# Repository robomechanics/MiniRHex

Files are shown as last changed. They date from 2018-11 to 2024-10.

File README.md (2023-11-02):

# MiniRHex: An Open-Source Hexapod Robot

[Contact Info](https://www.cmu.edu/me/robomechanicslab/contact.html)

MiniRHex is a miniature-scale hexapod designed by the [Robomechanics Lab](https://www.cmu.edu/me/robomechanicslab/) based on the design of the cockroach-inspired [RHex](https://repository.upenn.edu/handle/20.500.14332/34172). Notable features include a 3D printed chassis and legs for low cost construction and an intuitive software package that allows for highly-customizable control over the robot’s behavior. MiniRHex is designed to be an educational and outreach tool enabling students to experiment with a fully functional walking robot at a much lower cost. The low price tag lets research groups maintain a fleet of machines, allowing each student more hands-on interaction with the hardware. Possible educational principles include gait design and optimization, leg design and control, and mobile robot sensor incorporation.

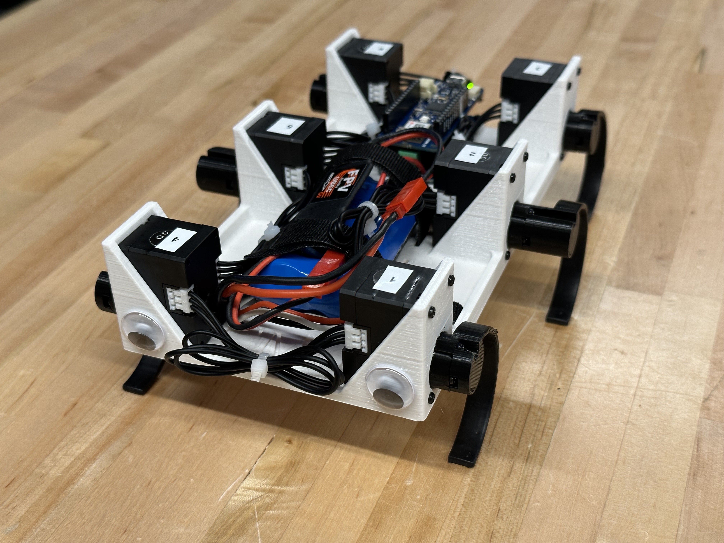
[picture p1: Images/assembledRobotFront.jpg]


# Setup Instructions
Building a MiniRHex requires access to a 3D printer. The links for off the shelf parts can be found below.

## Acquire Parts
The Parts List and Links to order can be found in [Parts List](HardwareList).

## Assemble Robot
Assembly Instructions are available at [Assembly Instructions](Assembly).

## Install Software
1. Install the Arduino IDE from https://www.arduino.cc/en/software
2. Open the Arduino IDE and under "Tools" select "Manage Libraries..."
   - Type "DynamixelShield" into the search bar
   - Select "Install" for the DynamixelShield library
3. Under "Tools" hover over "Board" and select "Boards Manager..."
   - Type "Arduino SAMD Boards" into the search bar
   - Select "Install" for the Arduino SAMD Boards (32-bits ARM Cortex-M0+)
4. (Non-developers) Download the [MiniRHex repository](https://github.com/robomechanics/MiniRHex/archive/refs/heads/main.zip) and extract the downloaded zip file
5. (Developers) Clone the MiniRHex repository from https://github.com/robomechanics/MiniRHex.git

# Operating Instructions
## Upload Code
1. Connect the MiniRHex to your computer via the Micro USB port
2. Open MiniRHex.ino (located in the MiniRHex subfolder) in the Arduino IDE and check that under "Tools":
   - "Board" is set to "Arduino MKR WiFi 1010" (under "Arduino SAMD (32-bits ARM Cortex-M0+) Boards")
   - "Port" is set to the correct COM port, e.g. "COM# (Arduino MKR WiFi 1010)"
3. Upload code to the robot (the circular button near the top left with an arrow pointing to the right)
4. Insert a fully charged battery, fasten the velcro straps, connect the voltage monitor, and connect the battery cable
5. Open the Serial Monitor in the Arduino IDE (the circular button in the top right with a magnifying glass)
6. Type "w" into the text box and hit enter to start walking! ("q" to stop, "s" to reverse", "a" to turn left, "d" to turn right)
7. To modify the walking gait, go to the "gait_parameters.cpp" tab in the Arduino IDE and edit the parameters for each leg, then upload code again (see comments in the file for more details)
8. When finished, unplug the battery and store it in a fireproof container (never leave a battery in the robot!)

## Connect to Wi-Fi
1. After uploading code, the LED on the Arduino will turn green and the Serial monitor should initially print the following message:
> Starting WiFi network...  
> SSID: minirhex    
> Website: http://10.0.0.1
2. Connect to the wifi network listed after "SSID" from your phone or computer. The LED on the Arduino will turn blue and start flashing.
3. On your device, navigate to the provided website. Make sure to use http, not https.
4. Use the buttons or the indicated keys to wirelessly control the robot!

# Robot Specifications
| | MiniRHex | X-RHex (2010) |
|---|---|---|
| Mass | 0.40 kg | 8.6 kg |
| Carrying Capacity [^1]| 1.8-3 kg | 5-10 kg |
| Length | 0.186 m | 0.53 m |
| Width | 0.100 m | 0.39 m |
| Leg Diameter | 0.064 m | 0.175 m |
| Leg Spring Constant | 0.3 N/mm | 1.4-1.7 N/mm |
| Leg Actuation | Dynamixel XL330 Servo | Maxon Brushless Motor |
| Onboard Processor | Arduino MKR WiFi 1010 | PC104, Intel Atom |
| Single Unit Price | <$300 | ~$20,000 |

[^1]: Evaluated using legs with higher spring constant

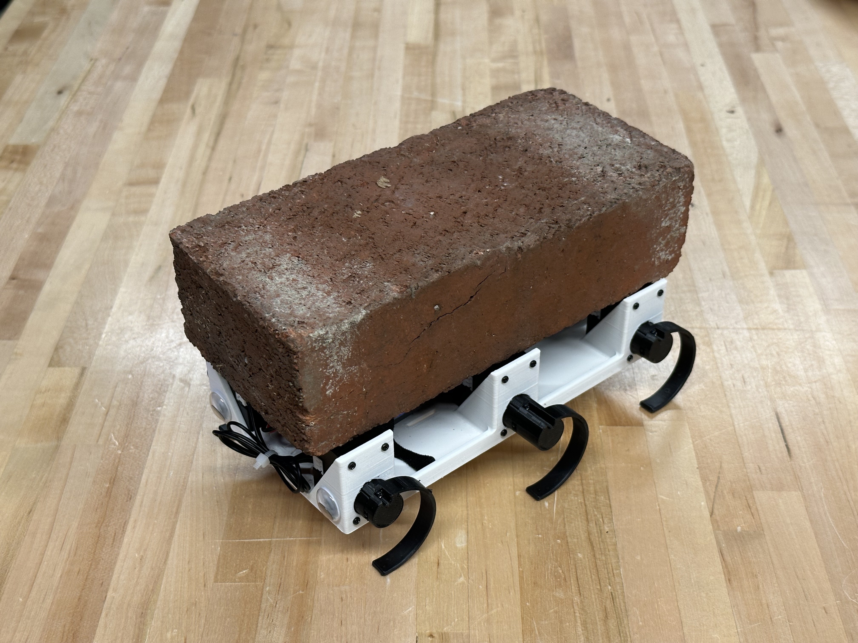
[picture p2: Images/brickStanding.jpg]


# Useful Links
### Parts List
The part list can be found at [Parts List](HardwareList).
### MiniRHex Repository
The MiniRHex repository can be found at [MiniRHex Repository](https://github.com/robomechanics/MiniRHex.git).
### Cite MiniRHex
If referencing MiniRHex in a paper, please cite [this abstract](http://www.andrew.cmu.edu/user/amj1/papers/RSS2018ws_MiniRHex.pdf).
Use [this BibTeX](/citation.txt) for citations:
> M. Barragan, N. Flowers, and A. M. Johnson. "MiniRHex: A Small, Open-source, Fully Programmable Walking Hexapod". In *Robotics: Science and Systems Workshop on ``Design and Control of Small Legged Robots''*, Pittsburgh, PA, June 2018.

### Images
See the [image gallery](Images) for more MiniRHex pictures.
        
### Videos
Check out the Robomechanics Lab [YouTube Page](https://www.youtube.com/watch?v=ldLXVDNCCzc&list=PLxHmBiQi0bD2aFgPKIrXhYXCCOGhTQmmk) for videos of MiniRHex in action!

# Contributors
MiniRHex was designed by the following people in the [Robomechanics Lab](https://www.cmu.edu/me/robomechanicslab/)
* Nikolai Flowers (BS ME '20)
* Barrett Werner (MS ME '19)
* Monica Barragan (BS ME '19)
* Cameron Selby (MS ME '18)
* Scott Phillips (BS ME '20)
* J. Joe Payne (Ph.D ME)
* Joe Norby (Ph.D ME '22)
* Catherine Pavlov (Ph.D ME '23)
* Paul Nadan (Ph.D RI)
* Aaron Johnson (Advisor)

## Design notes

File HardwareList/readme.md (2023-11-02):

# Hardware List

| Supplier | Item | Quantity | Price | Link |
|---|---|---|---|---|
| **Amazon** | Arduino MKR WiFi 1010  | 1 | $39.99 | [Amazon](https://www.amazon.com/Arduino-MKR-WiFi-1010-ABX00023/dp/B07FYFF5YZ) |
| | Batteries and charger  | 1 (2 batteries) | $22.99 | [Amazon](https://www.amazon.com/1500mAh-Li-ion-Battery-Helicopter-Charger/dp/B089W89KCP) |
| | Plastidip | 1 (per 5 robots) | $19.00 | [Amazon](https://www.amazon.com/Plasti-Dip-Multi-Purpose-Coating-Aerosol/dp/B07QCPXXBV) |
| | JST Plug Connectors | 1 (per 10 robots) | $6.29 | [Amazon](https://www.amazon.com/eBoot-Connector-Female-Cable-Battery/dp/B01M5AHF0Z) |
| | 5V UBEC | 1 (per 2 robots) | $11.69 | [Amazon](https://www.amazon.com/ShareGoo-Converter-Module-Quadcopter-Holder/dp/B07DYXTX9H) |
| | 8"x1/2" Velcro Straps  | 1 (per 8 robots) | $8.18 | [Amazon](https://www.amazon.com/VELCRO-Brand-Reusable-Fastening-Organizing/dp/B0006BB9MG) |
| | LiPo Voltage Monitor | 1 | $5.49 | [Amazon](https://www.amazon.com/Battery-Monitor-Voltage-Checker-Indicator/dp/B013U1CP08) |
| | LiPo Safe Bag | 1 (per 8 batteries) | $10.99 | [Amazon](https://www.amazon.com/DerBlue-Fireproof-Explosionproof-Battery-Bag185x75x60mm/dp/B01GCHBQJS/) |
| **Robotis** | Arduino Shield | 1 | $19.10 | [Robotis](https://www.robotis.us/dynamixel-shield-for-arduino-mkr-series/) |
| | Dynamixel XL330-M077-T | 6 | $143.40 | [Robotis](https://www.robotis.us/dynamixel-xl330-m077-t/) |
| **3D Print** | Robot Body | 1 | | [STL File](../CAD/STL/robot_body.STL) |
| | Front & Rear Left Legs | 2 | | [STL File](../CAD/STL/standard_leg_left.STL) |
| | Front & Rear Right Legs| 2 | | [STL File](../CAD/STL/standard_leg_right.STL) |
| | Middle Left Leg | 1 | | [STL File](../CAD/STL/standard_leg_left_middle.STL) |
| | Middle Right Leg | 1 | | [STL File](../CAD/STL/standard_leg_right_middle.STL) |
| | PLA Filament | ~120g PLA | ~$3.00 | [Amazon](https://www.amazon.com/HATCHBOX-3D-Filament-Dimensional-Accuracy/dp/B015I1CZUI) |
| **Total Cost** | | 1 robot | **$290.12** | (as of 10-27-23) |

[Return to homepage](../).

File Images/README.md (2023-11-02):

# MiniRHex Image Gallery

MiniRHex Front View

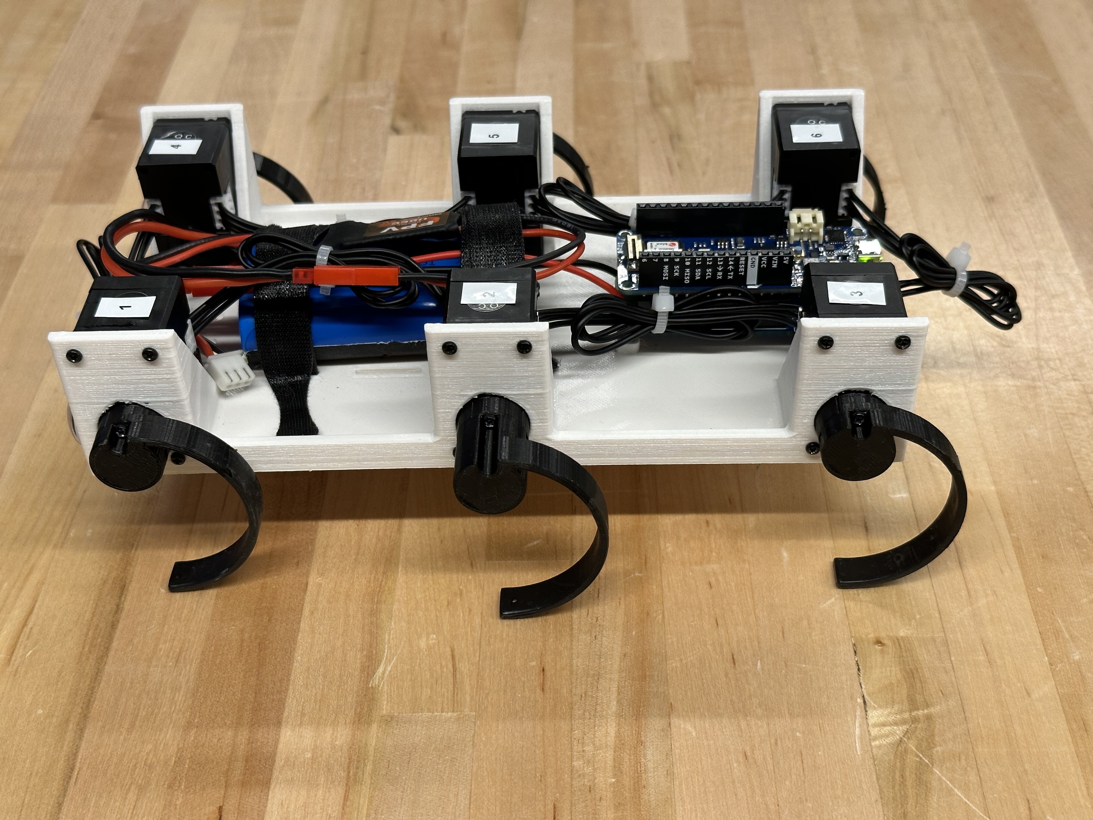
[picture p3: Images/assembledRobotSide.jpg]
MiniRHex Side View


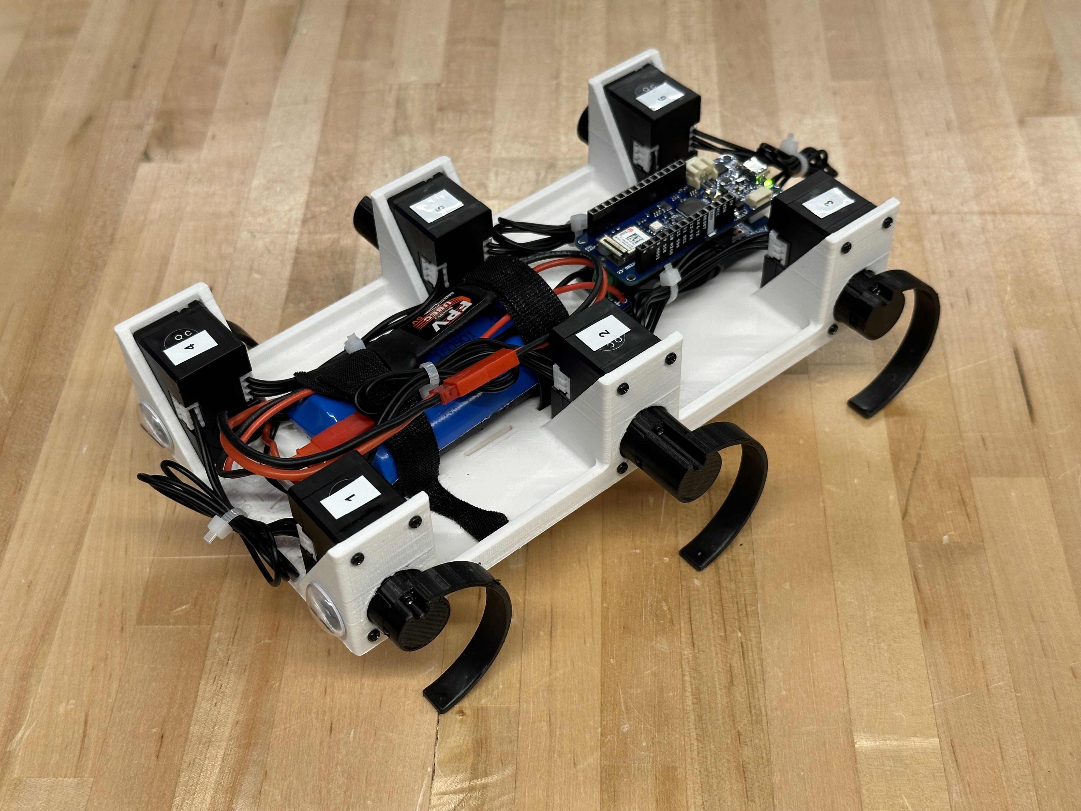
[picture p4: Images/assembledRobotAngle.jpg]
MiniRHex Above View


MiniRHex Carrying Brick

[Return to homepage](../).

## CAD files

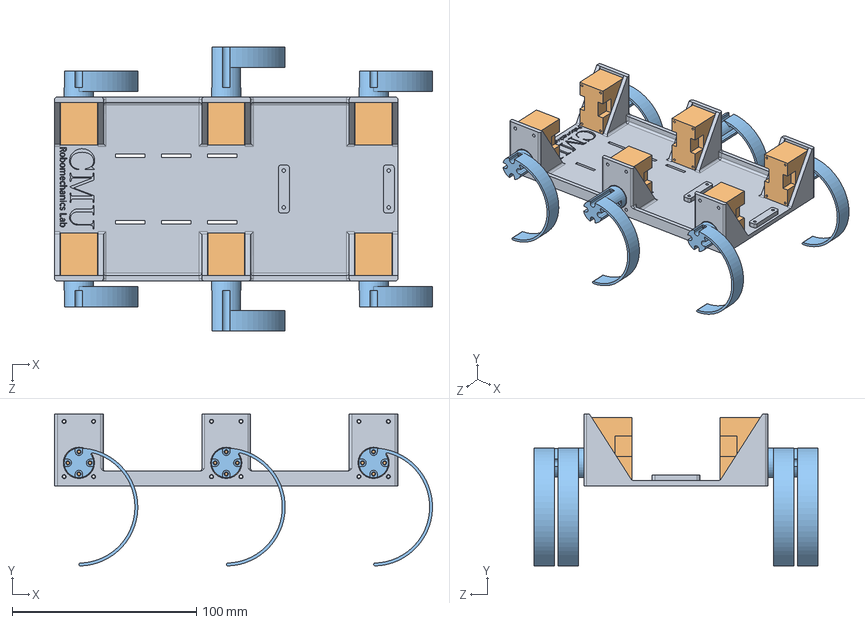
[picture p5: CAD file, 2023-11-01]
CAD/minirhex_assembly.SLDASM
205.2 x 82.5 x 154.0 mm
robot_body
dxl_XL-330 x 6
standard_leg x 6

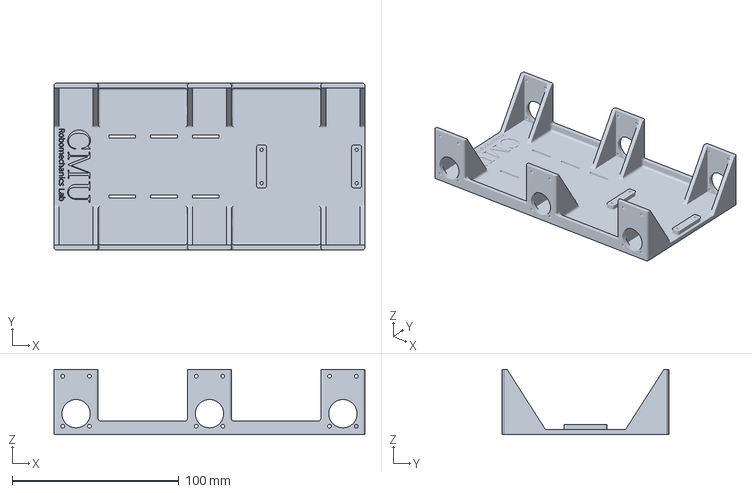
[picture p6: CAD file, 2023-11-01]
CAD/Prusa/robot_body.3mf
186.5 x 100.0 x 39.0 mm

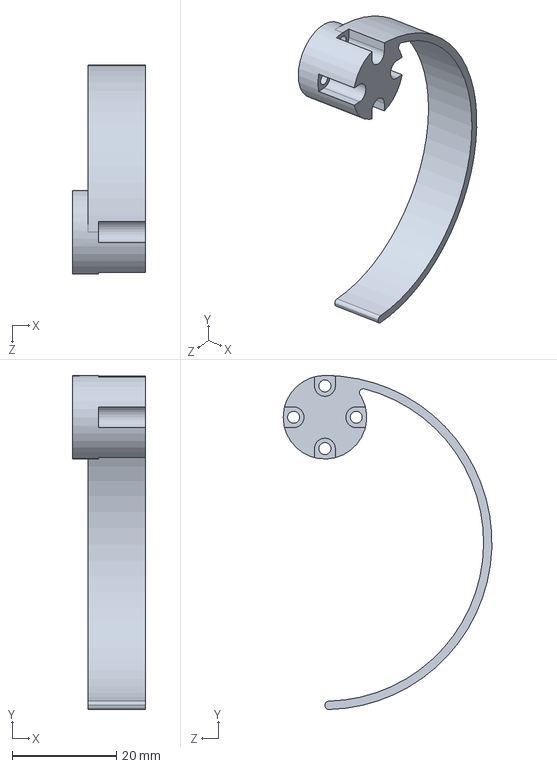
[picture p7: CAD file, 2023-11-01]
CAD/standard_leg.SLDPRT
14.0 x 64.0 x 40.0 mm

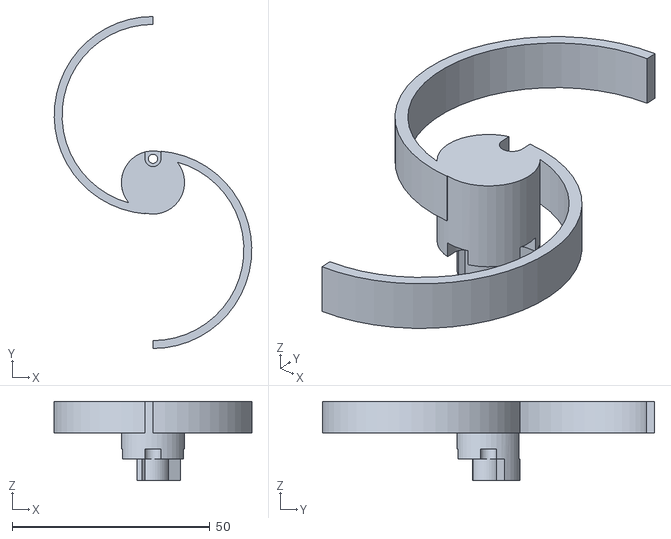
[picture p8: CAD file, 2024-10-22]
CAD/STL/quick_connect_leg_double_middle_left.STL
50.0 x 84.0 x 20.0

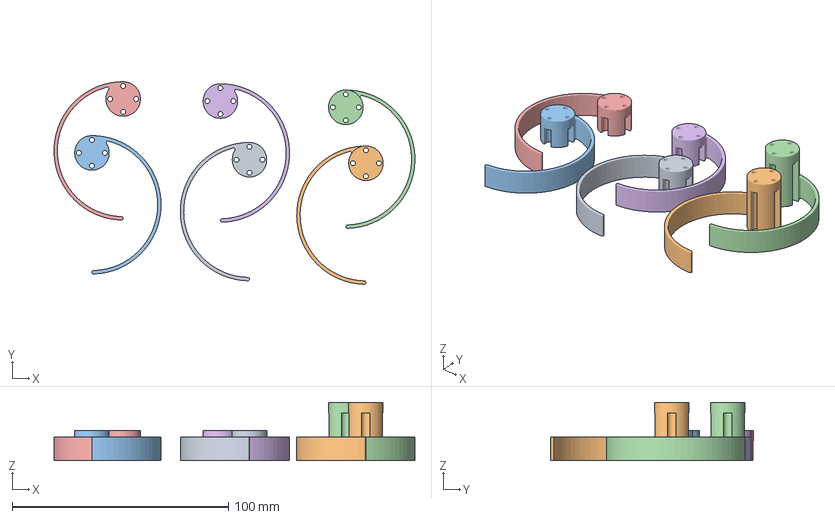
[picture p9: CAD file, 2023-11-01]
CAD/Prusa/standard_legs.3mf
166.9 x 93.7 x 27.0 mm
standard_leg_left.STL x 2
standard_leg_left_middle.STL
standard_leg_right.STL x 2
standard_leg_right_middle.STL

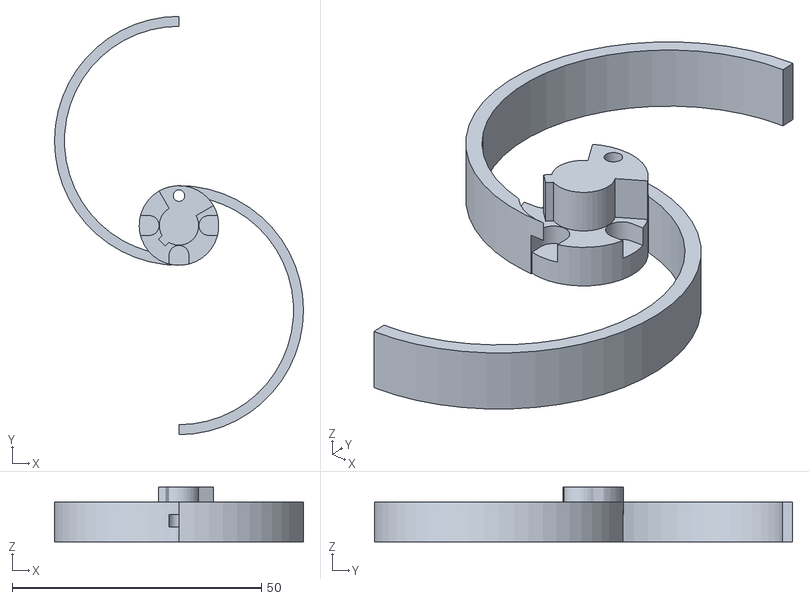
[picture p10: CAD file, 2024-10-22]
CAD/STL/quick_connect_leg_double_right.STL
50.0 x 84.0 x 11.0

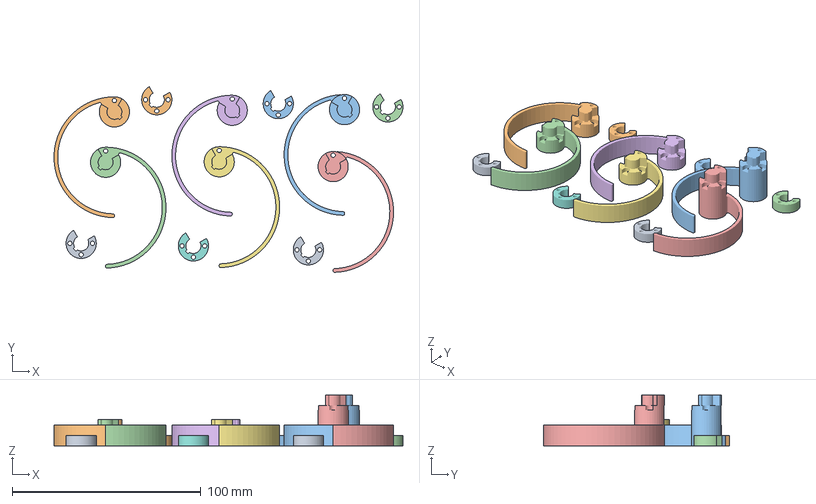
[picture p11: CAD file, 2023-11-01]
CAD/Prusa/quick_connect_legs.3mf
184.8 x 98.3 x 27.0 mm
quick_connect_hub.STL x 6
quick_connect_leg_left.STL x 2
quick_connect_leg_left_middle.STL
quick_connect_leg_right.STL x 2
quick_connect_leg_right_middle.STL

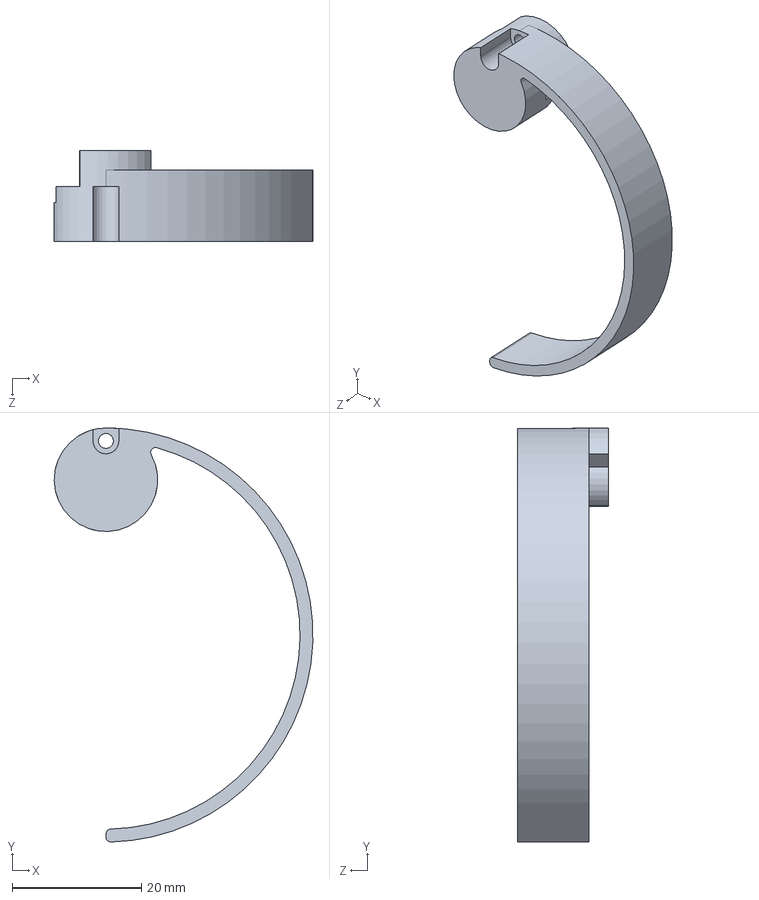
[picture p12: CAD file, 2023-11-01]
CAD/quick_connect_leg.SLDPRT
40.0 x 64.0 x 14.0 mm

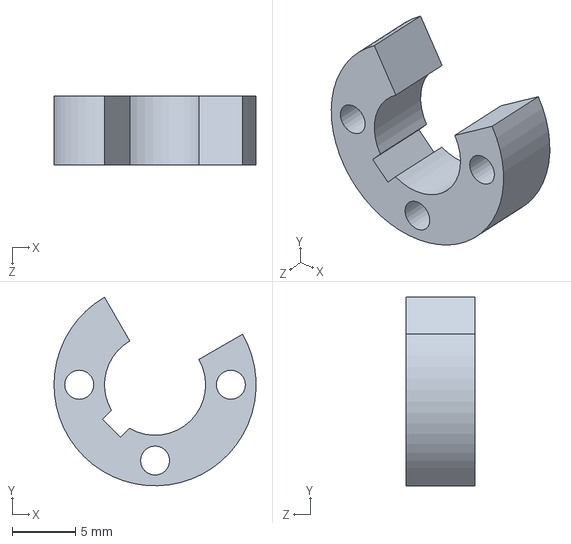
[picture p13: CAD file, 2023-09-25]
CAD/quick_connect_hub.SLDPRT
16.0 x 14.9 x 5.50 mm

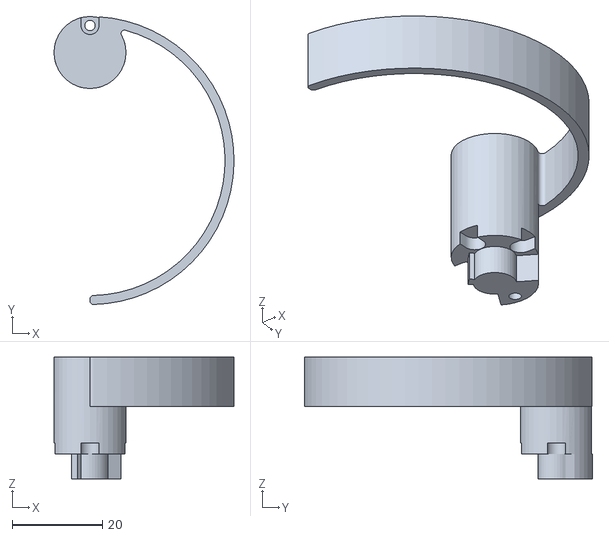
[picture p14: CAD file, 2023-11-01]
CAD/STL/quick_connect_leg_left_middle.STL
40.0 x 64.0 x 27.0

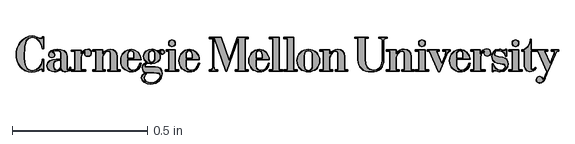
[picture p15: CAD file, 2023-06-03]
CAD/cmu-wordmark-horizontal-k.dxf
2.01 x 0.178 in

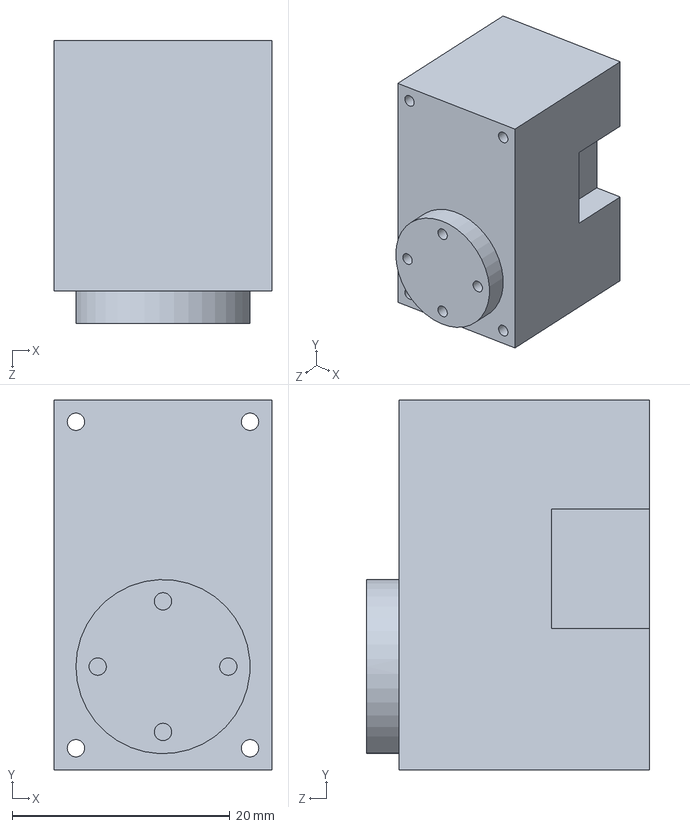
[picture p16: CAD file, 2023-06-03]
CAD/dxl_XL-330.SLDPRT
20.0 x 34.0 x 26.0 mm

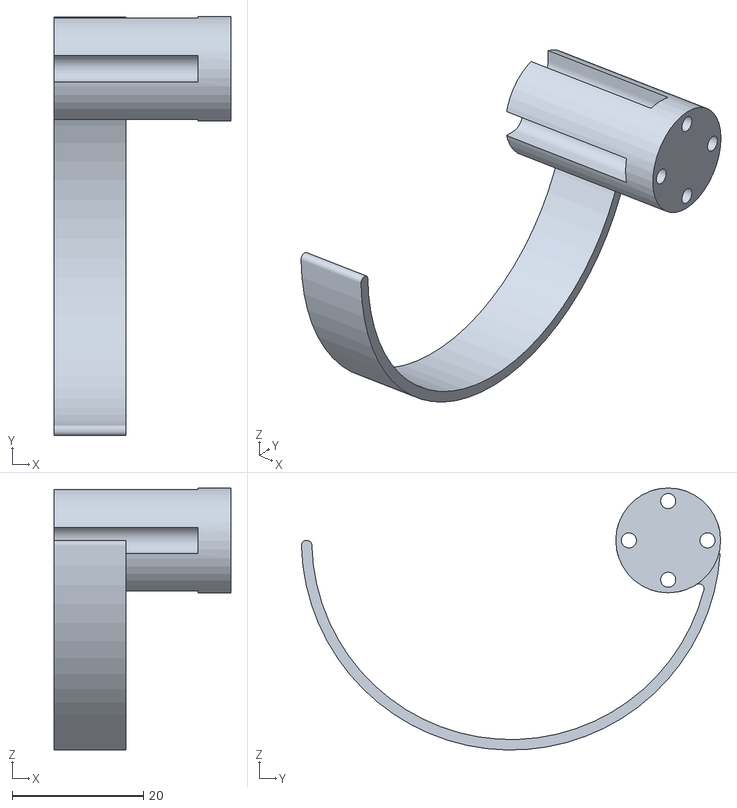
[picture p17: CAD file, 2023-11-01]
CAD/STL/standard_leg_right_middle.STL
27.0 x 64.0 x 40.0

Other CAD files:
CAD/quick_connect_leg_double.SLDPRT
CAD/STL/quick_connect_leg_double_left.STL
CAD/STL/quick_connect_leg_double_middle_right.STL
CAD/STL/quick_connect_leg_right_middle.STL
CAD/robot_body.SLDPRT
CAD/STL/quick_connect_hub.STL
CAD/STL/quick_connect_leg_left.STL
CAD/STL/quick_connect_leg_right.STL
CAD/STL/robot_body.STL
CAD/STL/standard_leg_left.STL
CAD/STL/standard_leg_left_middle.STL
CAD/STL/standard_leg_right.STL
CAD/rml-logo-robots-black.dxf

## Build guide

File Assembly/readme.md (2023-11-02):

# Preparation
1. Acquire the following equipment.
    * 3D printer + PLA filament
    * Wire cutters
    * Small Phillips head screwdriver
    * Small flat head screwdriver (basic users only)
    * Soldering station (advanced users only)

2. Purchase necessary components from the [Hardware List](../HardwareList).
    * Amazon: Arduino MKR, Battery, Plastidip, JST Connector, 5V UBEC, Velcro Straps, LiPo Voltage Monitor, and LiPo Safe Bag
    * Robotis: Dynamixel Servos, Arduino Shield

# Fabrication
1. 3D print the following parts. STL files can be found in [CAD/STL](https://github.com/robomechanics/MiniRHex/tree/main/CAD/STL) and SolidWorks files are provided in [CAD](https://github.com/robomechanics/MiniRHex/tree/main/CAD) to allow modification if needed. It is recommended to print with PLA, using the provided settings. Users of Prusa i3 MK3S 3D printers can also use the PrusaSlicer project files and g-code in the [CAD/Prusa](https://github.com/robomechanics/MiniRHex/tree/main/CAD/Prusa) folder. Make sure to remove any support material from the legs before assembly.

    * 1 robot body ([robot_body.STL](../CAD/STL/robot_body.STL)): 15%-20% infill, no supports
    * 2 standard left front/back legs ([standard_leg_left.STL](../CAD/STL/standard_leg_left.STL)): 100% infill, support on build plate
    * 2 standard right front/back legs ([standard_leg_right.STL](../CAD/STL/standard_leg_right.STL)): 100% infill, support on build plate
    * 1 standard left middle leg ([standard_leg_left_middle.STL](../CAD/STL/standard_leg_left_middle.STL)): 100% infill, support on build plate
    * 1 standard right middle leg ([standard_leg_right_middle.STL](../CAD/STL/standard_leg_right_middle.STL)): 100% infill, support on build plate

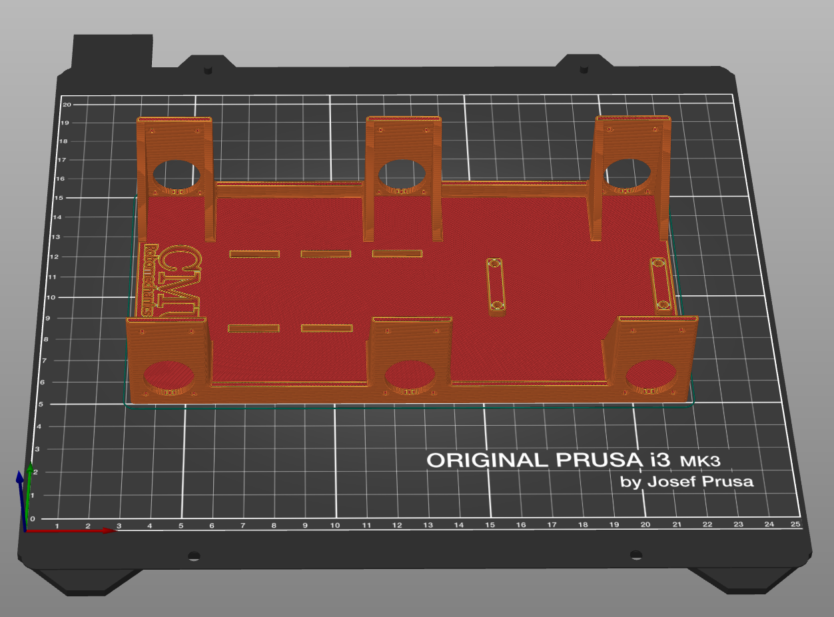
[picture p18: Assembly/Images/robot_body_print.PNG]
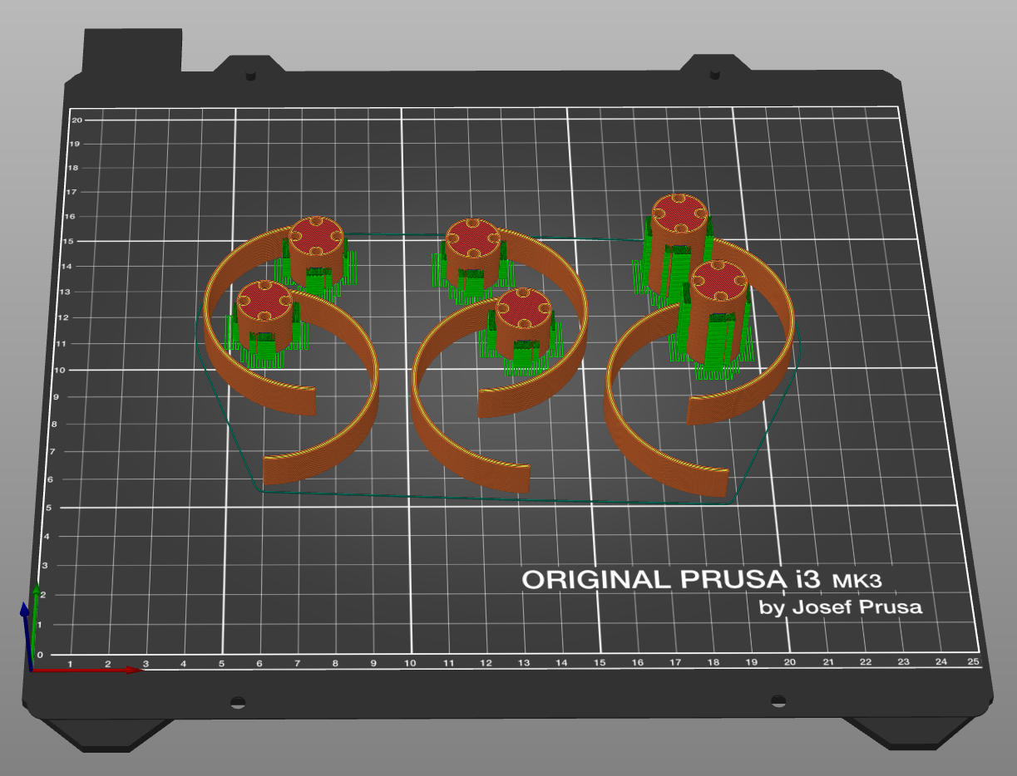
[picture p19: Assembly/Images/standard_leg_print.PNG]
      

    Certain users may desire to frequently switch out different legs, for which a quick-connect leg design is also available. The quick-connect legs are faster to swap, but less durable. Quick-connect leg users should instead print the following.

    * 1 robot body ([robot_body.STL](../CAD/STL/robot_body.STL)): 15%-20% infill, no supports
    * 2 quick-connect left front/back legs ([quick_connect_leg_left.STL](../CAD/STL/quick_connect_leg_left.STL)): 100% infill, support on build plate
    * 2 quick-connect right front/back legs ([quick_connect_leg_right.STL](../CAD/STL/quick_connect_leg_right.STL)): 100% infill, support on build plate
    * 1 quick-connect middle left leg ([quick_connect_leg_left_middle.STL](../CAD/STL/quick_connect_leg_left_middle.STL)): 100% infill, support on build plate
    * 1 quick-connect middle right leg ([quick_connect_leg_right_middle.STL](../CAD/STL/quick_connect_leg_right_middle.STL)): 100% infill, support on build plate
    * 6 quick-connect hubs ([quick_connect_hub.STL](../CAD/STL/quick_connect_hub.STL)): 100% infill, support on build plate

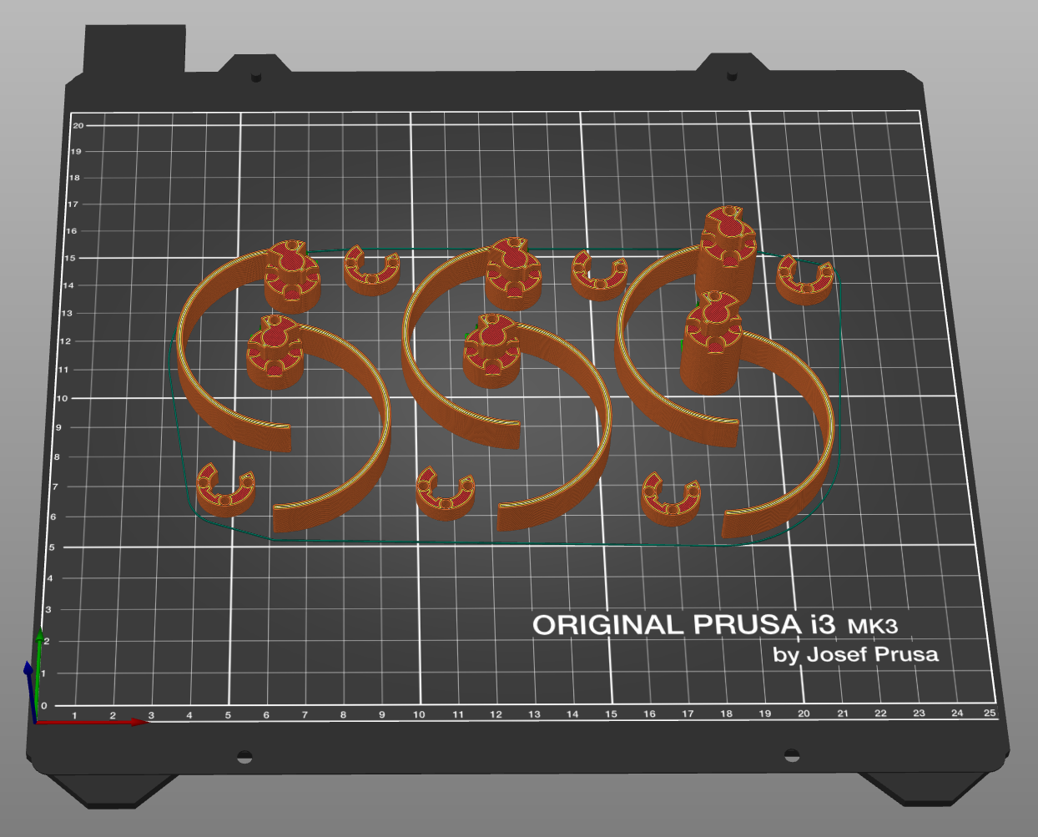
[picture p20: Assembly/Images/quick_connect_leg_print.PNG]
    

    Several additional leg variants exist, all compatible with the quick-connect system. For each additional set of legs you will need to 3D print 4 front/back legs and 2 middle legs of the appropriate type (but no additional hubs are needed).

2. Add Plastidip to legs for increased friction.
    * Use Plastidip (either dip or spray) to coat around 75% of each of the six legs until a high friction surface forms on each leg.
    * Between each coat, let dry for at least one hour.
    * Make sure the dip is evenly coated around the leg.
    * Do not cover the through holes for the screws.

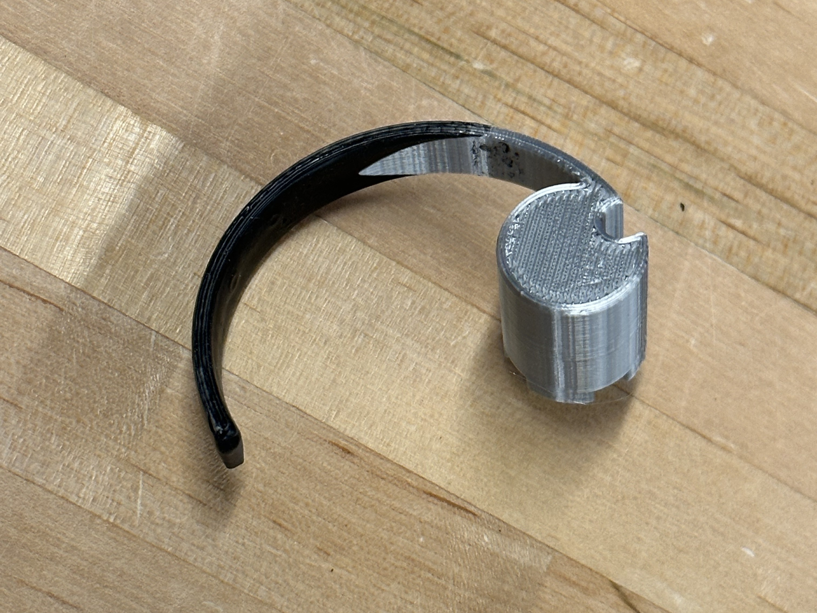
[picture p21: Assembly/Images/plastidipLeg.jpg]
    

# Assembly
1. Locate and sort motor screws.
    * Each of the motors comes with a set of screws. Open all six motor packages and sort into short and long screws.
    * You will need 4 short screws (M2x6) and 48 long screws (M2x8) to assemble the robot.
  
2. Mount the servos to the robot body.
    * Each motor requires 4 long screws. The screws will tap directly into the motor's plastic, so do not over tighten them.

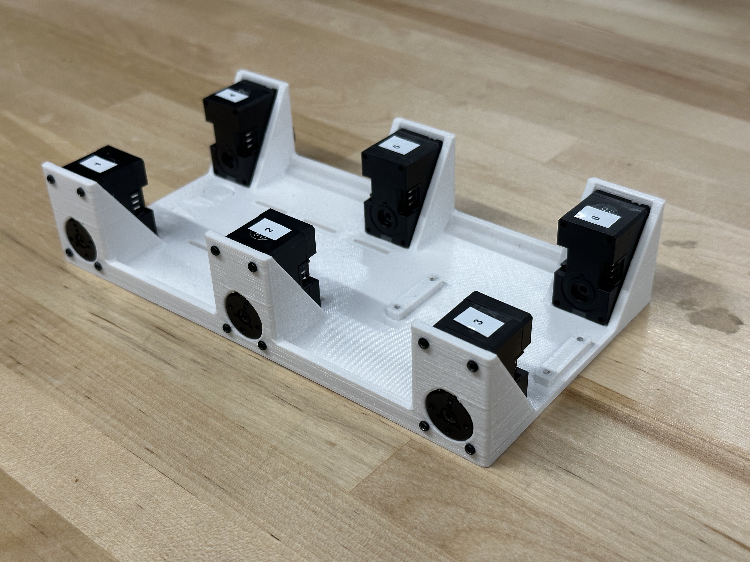
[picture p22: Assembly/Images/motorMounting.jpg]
    

3. Trim the leads on the Arduino shield.
    * The Robotis Arduino shield comes with leads that are too long. Using wire cutters, trim them to within 1-2mm of the board.
    * Only trim the leads on the shield, not the Arduino itself!

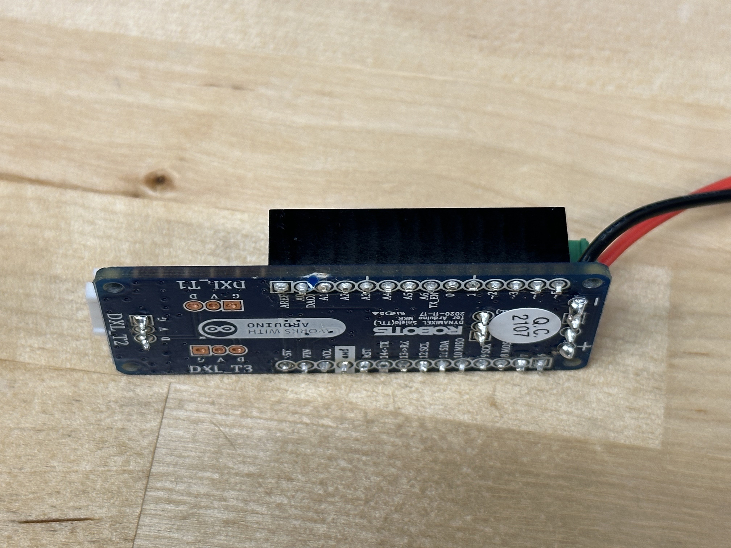
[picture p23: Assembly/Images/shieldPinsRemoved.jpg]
    

4. Attach the JST connector to the Arduino shield.
    * Basic users can insert the red and black wires into the green screw terminals (red goes into the + side, and black goes into the - side), then tighten them using the flat head screwdriver. Do not swap the colors, or it could severely damage the electronics!
    * Advanced users can instead solder the wires directly to the Arduino shield for a more robust connection, as pictured.

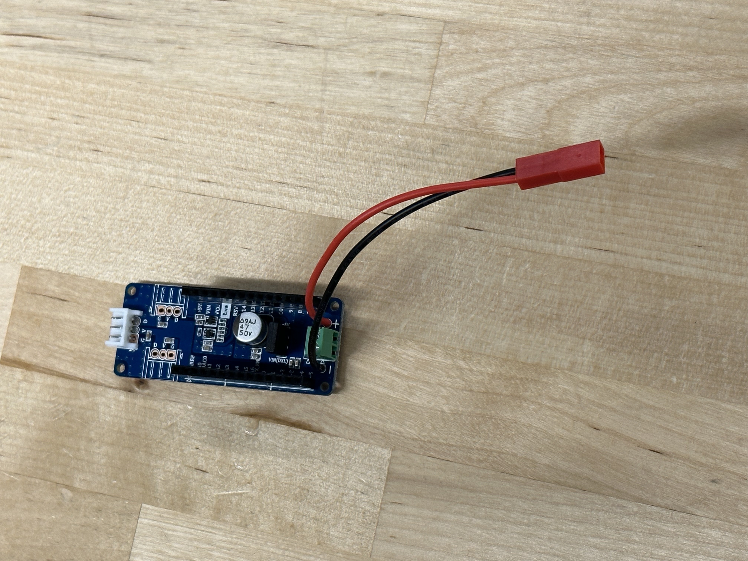
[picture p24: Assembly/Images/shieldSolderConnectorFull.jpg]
    

5. Mount the Arduino shield to the robot body.
    * You will needs 4 short screws. The screws will tap directly into the motor's plastic, so do not over tighten them.
    * The screw terminals and JST connector should face the center of the robot body.

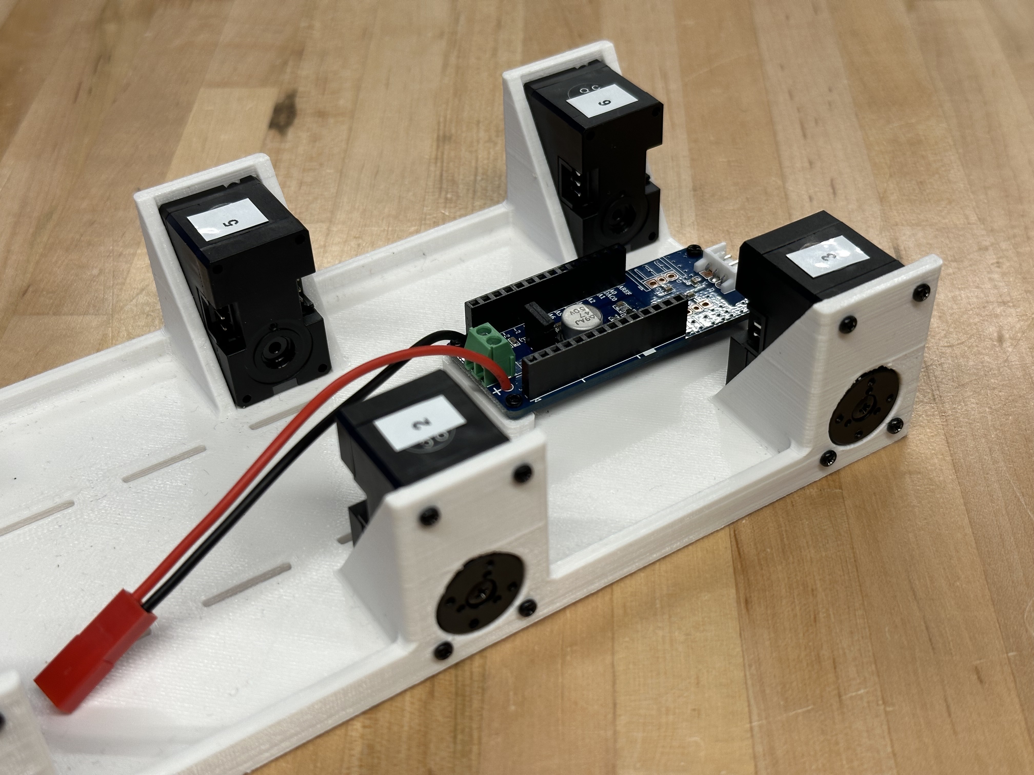
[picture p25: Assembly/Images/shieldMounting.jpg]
    

6. Stack the Arduino on top of the Arduino shield.
    * The header pins should line up, with the micro USB port facing the edge of the robot.

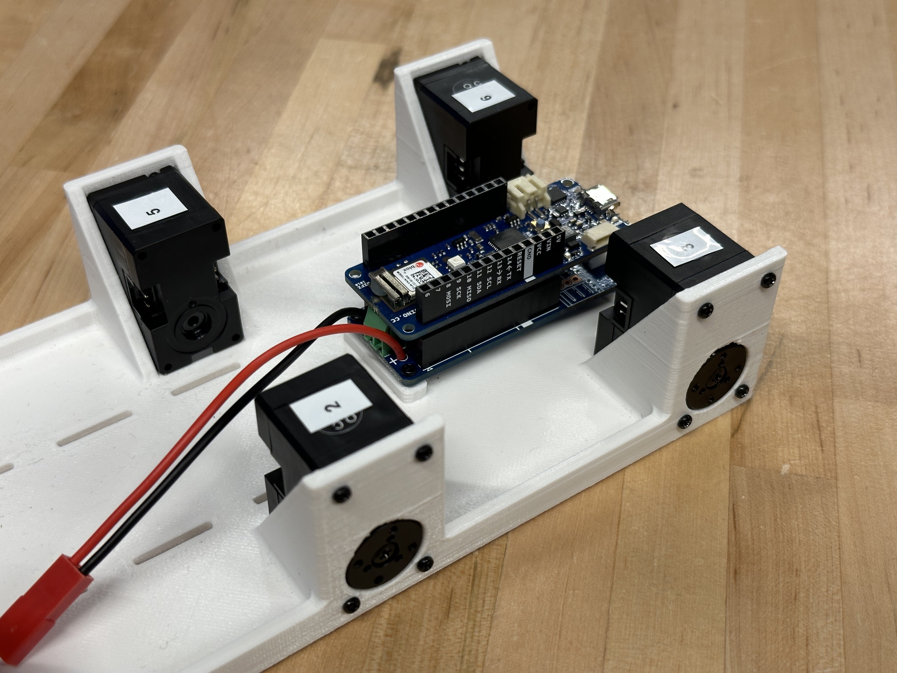
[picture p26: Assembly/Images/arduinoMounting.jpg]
    

7. Wire up the motors using the included Dynamixel cables.
    * The motors should be daisy-chained to each other in series, with the Arduino shield as one end of the chain.
    * A suggested ordering is: Arduino Shield -> Motor 6 -> Motor 5 -> Motor 4 -> Motor 1 -> Motor 2 -> Motor 3.
    * Use either the included wire wraps or zip ties to manage the wires, as pictured.

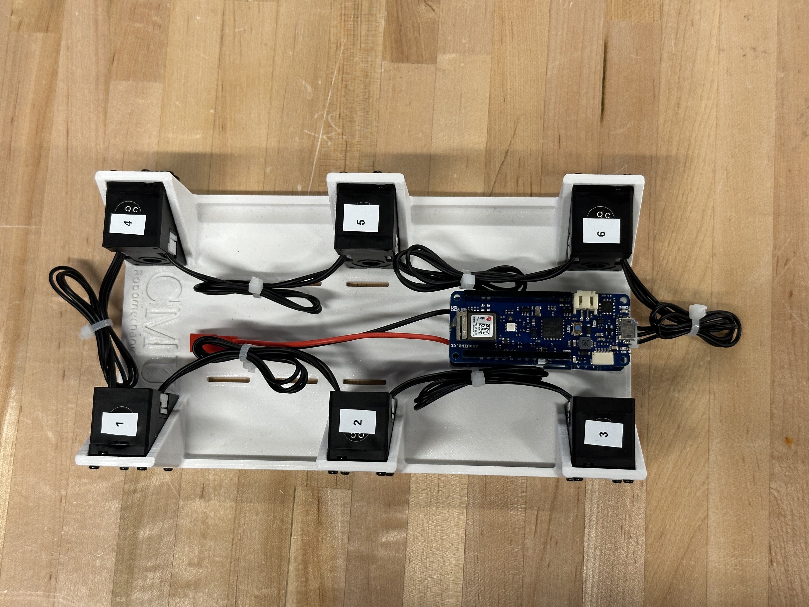
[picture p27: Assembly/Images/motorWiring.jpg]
    

8. Attach the 5V UBEC to the JST connector.
    * The JST connector is not reversible, so it will only connect if oriented correctly (red to red, black to black).

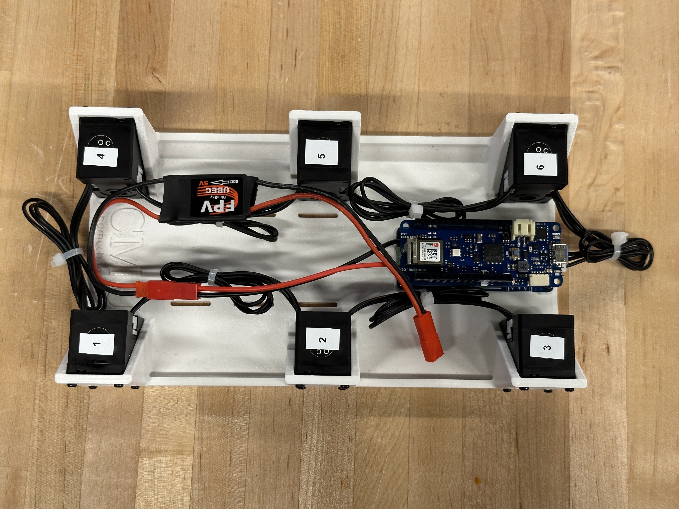
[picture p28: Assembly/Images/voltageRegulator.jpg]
    

9. Thread the Velcro straps through the slits in the robot body.
    * Ensure the ends of each strap come out on top of the robot body for ease of access.

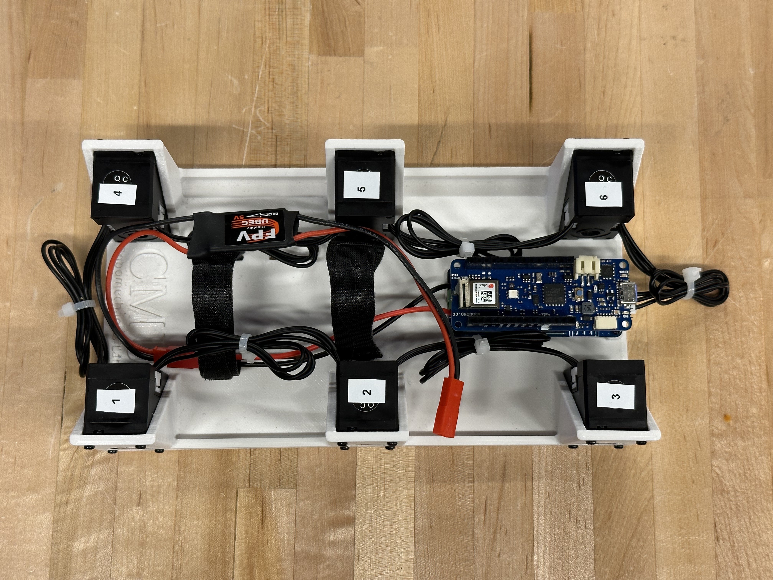
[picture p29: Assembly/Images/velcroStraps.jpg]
    

10. Align each servo horn.
    * Each servo horn has 3 small circular indents forming a triangle. Rotate the motor by hand until the circle closest to a screw mounting hole is at the top.

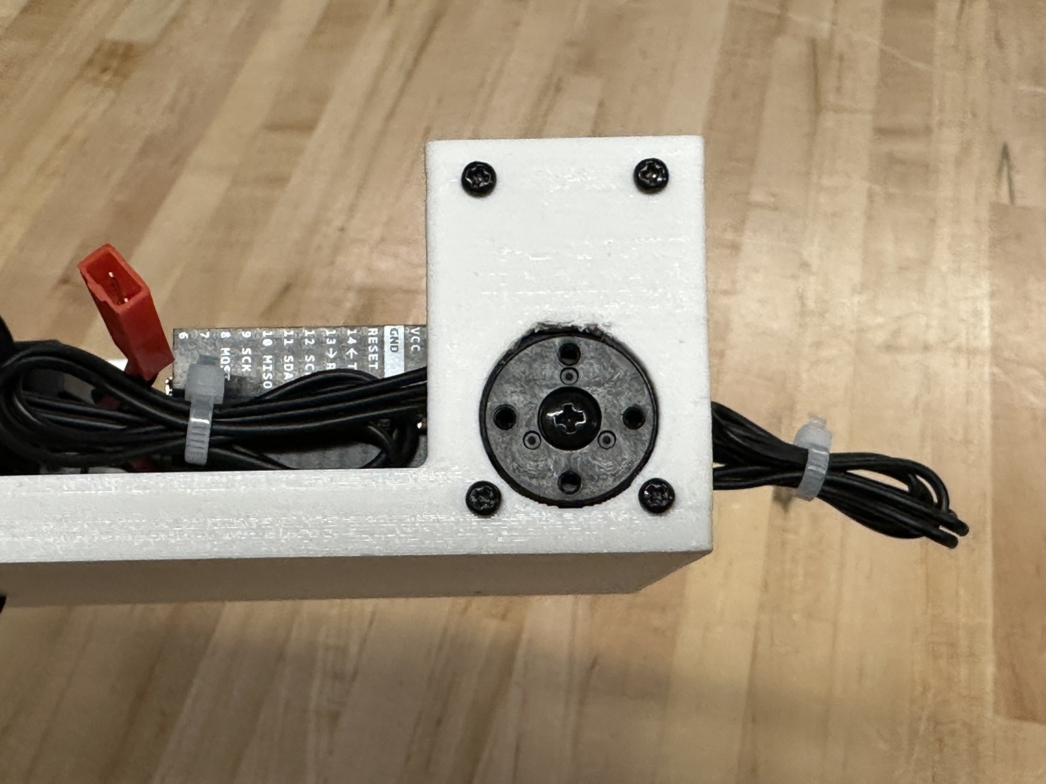
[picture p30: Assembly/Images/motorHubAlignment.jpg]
    

11. Mount a quick-connect hub to each servo horn (quick-connect leg users only).
    * Each quick-connect hub requires 3 long screws. The screws will tap directly into the motor's plastic, so do not over tighten them.
    * Ensure that the opening in the hub faces upwards, and the little notch in the hub is on the side closer to the front of the robot (the side without the Arduino).

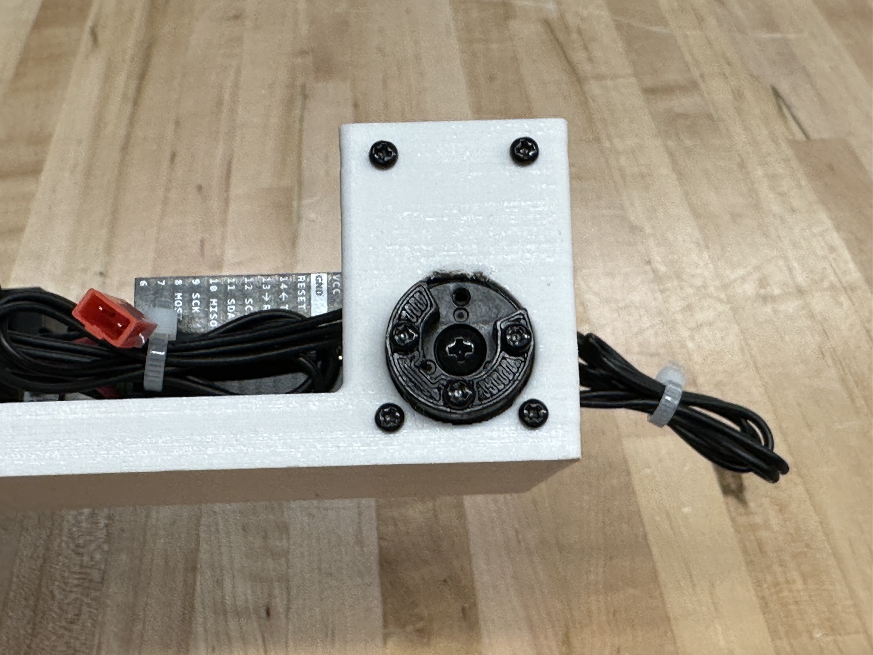
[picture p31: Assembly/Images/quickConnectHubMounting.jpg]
    

12. Mount a leg to each servo horn.
    * Quick-connect legs require 1 additional long screw, while standard legs require 4 long screws. The screws will tap directly into the motor's plastic, so do not over tighten them.
    * The middle legs extend out further from the robot, to prevent collisions between neighboring legs.
    * Ensure that the curved side of each leg faces the rear of the robot (the side with the Arduino) and the end of the leg is directly below the robot (with the servo horn aligned as in step 10), as pictured for both leg types.

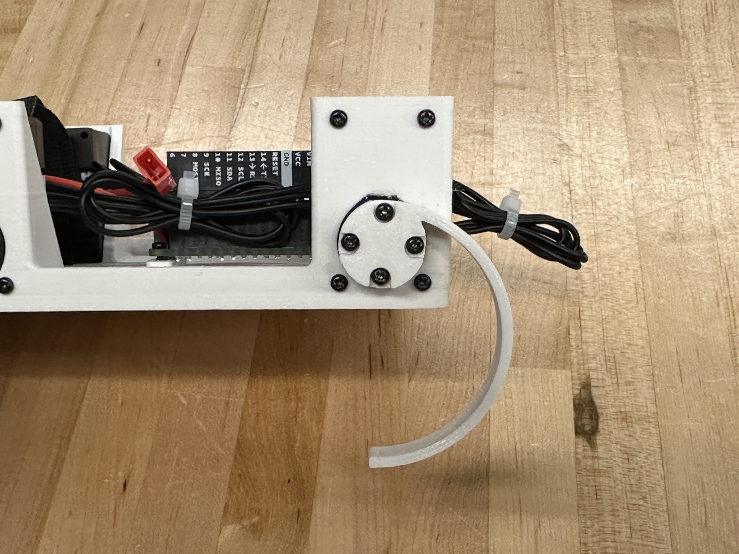
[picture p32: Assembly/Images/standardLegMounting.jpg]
    
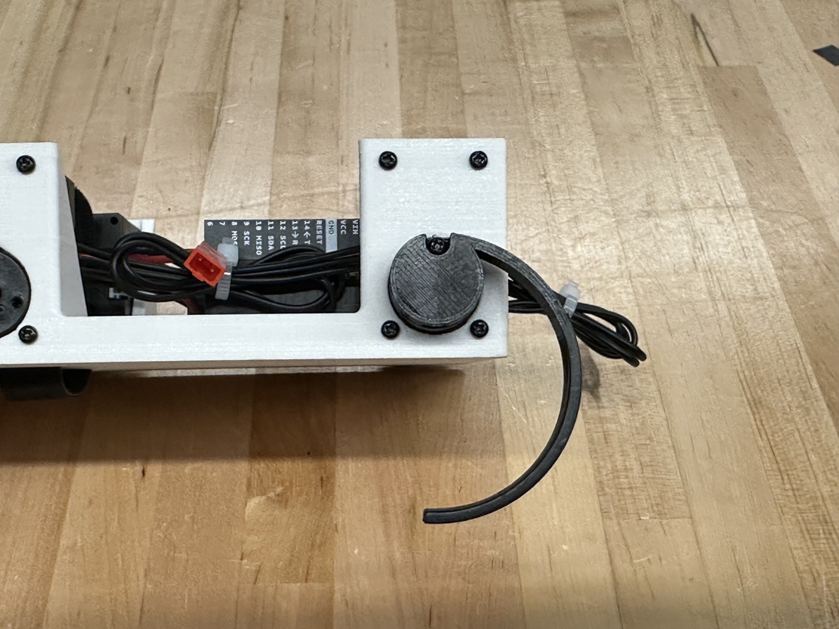
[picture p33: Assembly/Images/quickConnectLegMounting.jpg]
    
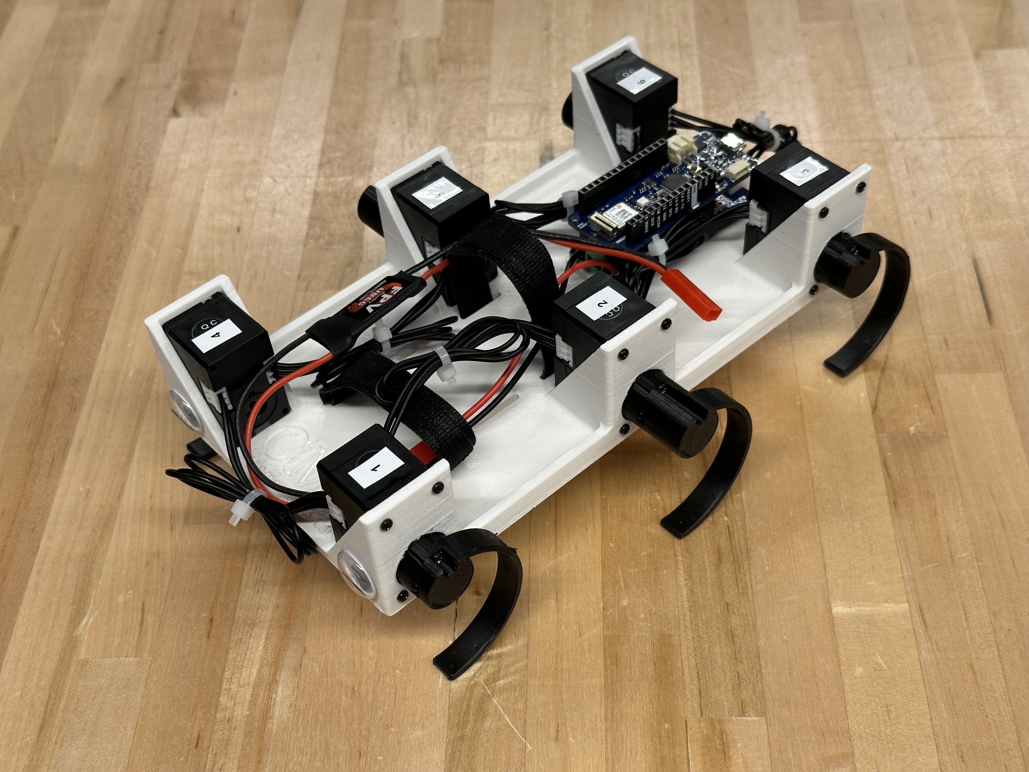
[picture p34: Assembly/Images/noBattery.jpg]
    

# Battery Usage
1. Fully charge a battery.
   * **WARNING: Improper handling of LiPo batteries is very dangerous and can cause fires.**
   * Never allow a battery to charge unsupervised.
   * When not in use, always store batteries in a LiPo safe bag or fireproof cabinet.
   * Carefully follow all instructions from the manufacturer of the battery and charger.
   * Safely dispose of batteries according to manufacturer instructions if the battery becomes puffy or if the voltage drops below 5V. Do not just throw LiPo batteries in the trash!

2. Connect the LiPo voltage monitor to the battery. Never run the robot without the voltage monitor connected!
   * The black wire on the white battery connector should plug into the minus port (far left) of the voltage monitor.
   * It is advised to cover the top of the voltage monitor with a finger while connecting it to the battery, to dampen the loud beep it produces.
   * The voltage monitor will sound an alarm if the battery dips below a safe level. When this happens, immediately unplug the battery from the robot and recharge it. Continuing to operate the battery below the safe voltage level will cause permanent damage, and possibly start a fire.
   * The maximum battery voltage is 8.4V, charge the battery if it falls below 7.0V, the alarm will sound at 6.6V, and dispose of the battery if it falls below 5.0V.

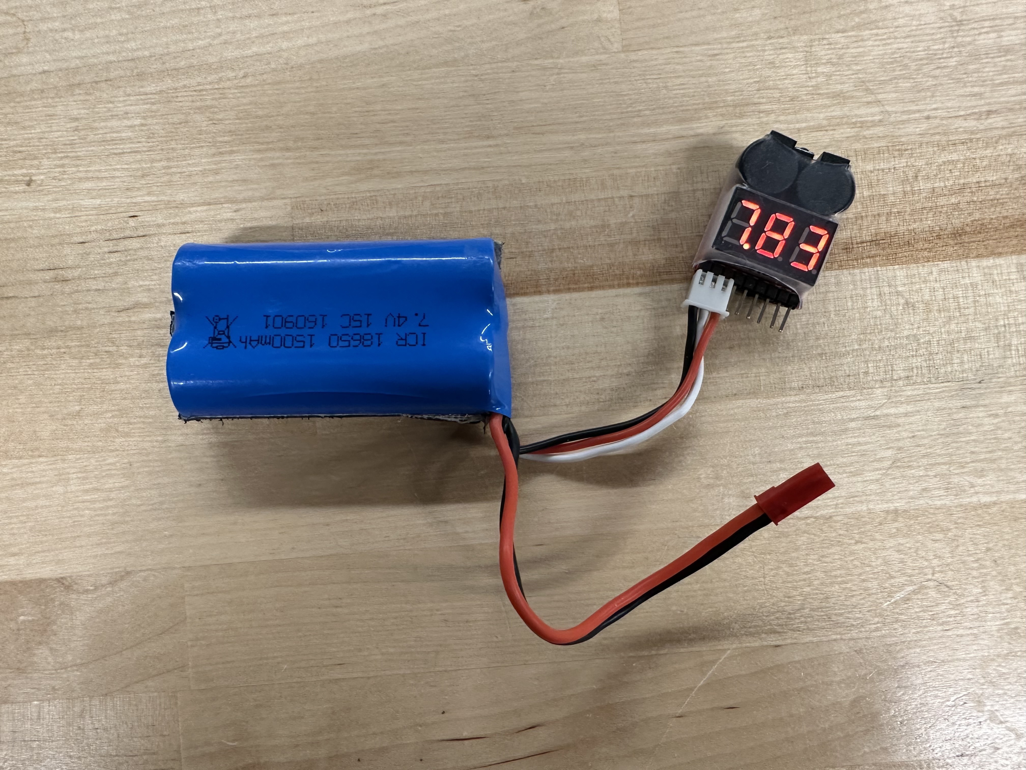
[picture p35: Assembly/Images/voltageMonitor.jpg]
   
   
3. Connect the battery to the robot.
   * Slide the battery through the Velcro straps, then tighten them to hold it in place.
   * Connect the battery to the 5V UBEC. Never connect the battery directly to the Arduino shield!

   

# Software Setup
1. Install the Arduino IDE and download the MiniRHex repository.
   * Instructions are available at [Install Software](../#install-software).

2. Configure the servo IDs for each leg. The correct Dynamixel servo positions are:
   - ID 1 = front left
   - ID 2 = center left
   - ID 3 = rear left
   - ID 4 = front right
   - ID 5 = center right
   - ID 6 = rear right

   To set the Dynamixel ID numbers, follow these steps:
   1. Disconnect all Dynamixel servos except for the one in position 2
   2. Open the Arduino IDE and check that under "Tools":
      - "Board" is set to "Arduino MKR WiFi 1010" (under "Arduino SAMD (32-bits ARM Cortex-M0+) Boards")
      - "Port" is set to the correct COM port, e.g. "COM# (Arduino MKR WiFi 1010)"
   3. Select "File" > "Examples" > "DynamixelShield" > "Basic" > "id" to open the ID-setting example script
   4. Find the line "new_id = DEFAULT_DXL_ID;" and delete it or comment it out: "// new_id = DEFAULT_DXL_ID;"
   5. Find the line "new_id = 100;" and edit it to "new_id = 2;"
   6. Upload code to the robot (the circular button near the top left with an arrow pointing to the right)
   7. Open the Serial Monitor in the Arduino IDE (the circular button in the top right with a magnifying glass) and verify the ID has been changed
   8. Unplug the Dynamixel and repeat from step 5 with the Dynamixel servos in positions 3, 4, 5 and 6 (setting "new_id = 3;" for ID 3, etc.)

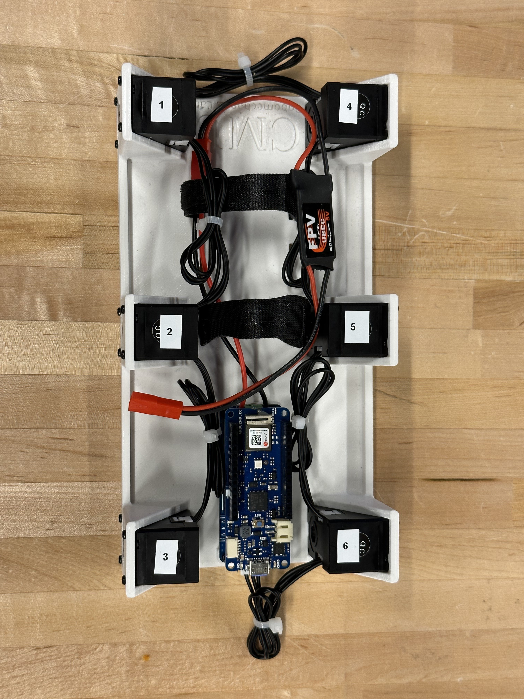
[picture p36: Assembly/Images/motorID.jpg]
   

3. Upload code using the micro-USB port. You can now operate the robot using the Serial Monitor or the web interface!
   * Instructions are available at [Operating Instructions](../#operating-instructions).

4. When finished, unplug the battery and store it in a fireproof container. Never leave a battery in the robot!

[Return to homepage](../).

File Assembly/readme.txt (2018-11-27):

MiniRHex Assembly Instructions

1. Solidworks files available in /CAD
    a. Any updated or changed SolidWorks parts will be uploaded here
  
2. Look at the MiniRhexHardware file to see the needed parts and links to the items.
    a. McMaster: M3 locknuts, button head screws, and spacer; 3mm acrylic
    b. Amazon: Battery, Plastidip, charger, and battery connectors
    c. Robotis: Main board, Dynamixels, Bluetooth(optional)
  
3. Print the following (PLA), .stl files can be found in /CAD/STL
    a. 6 servo sleeve parts, for best results print with the back side on the build plate 
    b. 4 shaft-edge parts
    c. 2 shaft-mid parts 
    d. 1 battery case part 
    e. 6 leg parts
    f. if you have access to an Ultimaker 3 Extended printer gcode can be found in /STL 
  
4. Open base.sldprt and save as a .dxf file. Use this file to laser cut 3-mm thick acrylic to
serve as the foundation for the robot.

5. Prepare the mainboard for use.
  a. Solder the battery connector onto one positive pinhole and one negative pinhole
  for power. The location on the board is shown below
  
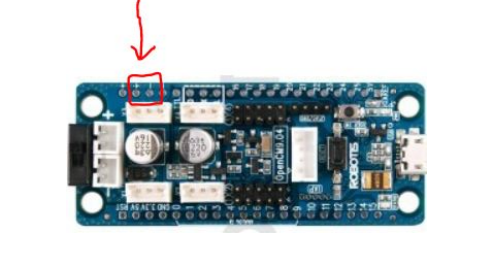
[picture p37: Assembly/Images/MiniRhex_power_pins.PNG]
Power pin location
  
  
6. First, connect the battery case and mainboard to the foundation, with the USB port facing outwards
  a. Connections:
    i. Battery case: M3 button head x 10 mm, M3 nut
    ii. Mainboard: M3 spacer, M3 button head x 10 mm, M3 lock nut
  b. Battery case is near the center of the foundation.
  c. The mainboard’s micro-USB port should face out.
  d. The mainboard will be towards the front of the robot.
  
7. Next, prepare the legs by using Plastidip (either dip or spray) and coating each of the six
legs until high friction surface forms on each leg.
  a. Between each coat, let dry for at least one hour.
  b. Make sure the dip is evenly coated around the leg.
  c. Do not cover the through holes for the screws.
  
8. Connect four of the six legs to edge shafts (shorter shafts).
  a. Align the leg through holes with the holes on the cut-out portion of the shaft.
  b. Connection: M3 socket head x 10 mm
  c. For two of the four connections, be sure to switch the orientation of the leg
  because those will be attached to the opposite side of the robot.
  
9. Connect the other two legs to the mid shafts (longer shaft).
  a. Align the leg through holes with the holes on the cut-out portion of the shaft.
  b. Connection: M3 socket head x 10 mm
  c. For one of the two connections, be sure to switch the orientation of the leg
  because those will be attached to the opposite side of the robot.
  
10.Connect each shaft-leg apparatus to the Dynamixel XL-320 servo motor.
  a. Orientation: Make sure the half circle each leg forms faces the front of the robot:
  towards the side with the mainboard.
  b. Detach the center screw in the servo horn, and pry off the horn itself.
    i. The horn looks like a small, black plastic cylinder.
  c. Align the 4 through holes on the servo horn with the 4 extruded pieces on the shaft
  face (the shaft length doesn’t matter).
  d. Align the horn (now connected to the leg apparatus) to its key on the body of the servo.
    i. Once the horn is flush against the body, connect the horn/shaft/leg apparatus
    to the servo motor.
    ii. Connection: center screw that came with the servo

12.Slide each servo into a servo sleeve.

13.Connect each servo sleeve to the foundation.
  a. Orientation: Be sure all legs face forward (semicircle faces the mainboard).
  b. Connection: M3 button head x 10 mm, M3 nut
  
14.Connect the servos to the mainboard.
  a. Connect such that no wires interfere with leg rotation.
15. Charge battery(ies) and check voltage(s).

16.Upload code using the micro-USB port.

17.Take electronic wires that come with the servos, and connect them like below

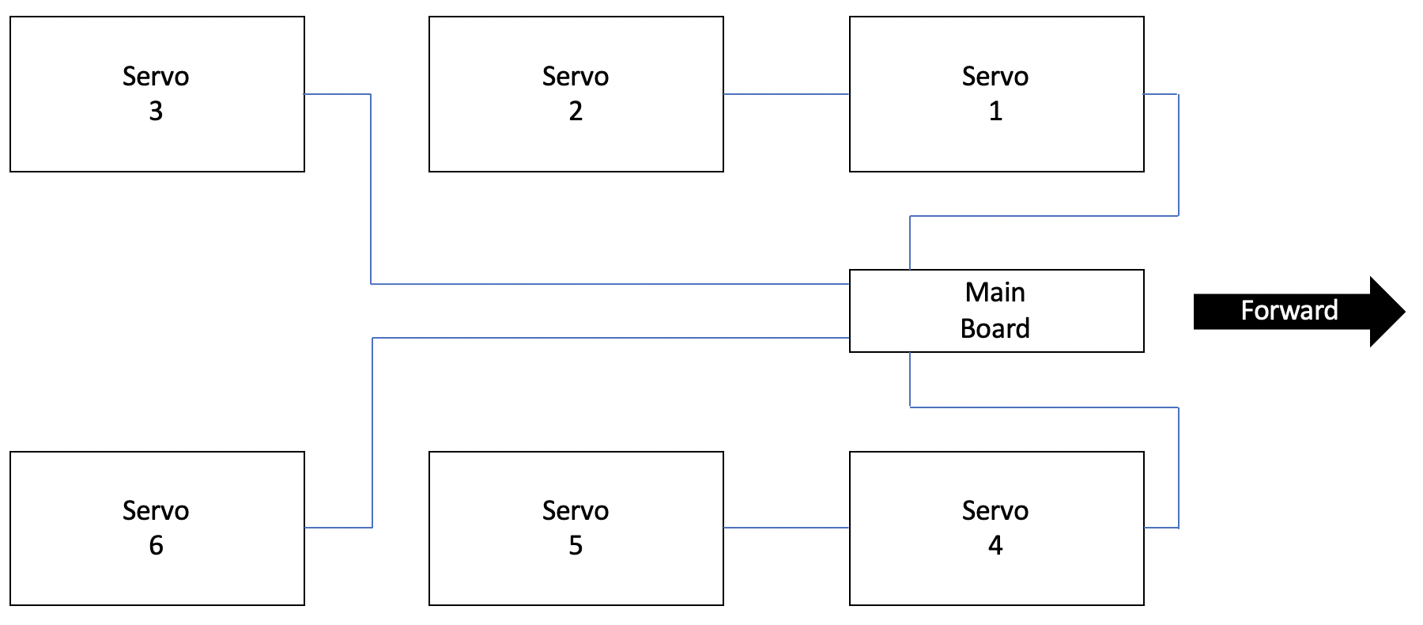
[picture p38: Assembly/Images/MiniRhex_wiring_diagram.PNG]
wiring diagram


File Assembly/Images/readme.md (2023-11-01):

Reference images for assembly instructions

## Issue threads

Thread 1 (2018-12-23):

Original servo horn screws too short

nitrovent, 2018-12-23:
I am trying to assemble a leg-shaft-servo-part but running into issues connecting the shaft to the servo.
(Step 10 of https://github.com/robomechanics/MiniRHex/tree/master/Assembly)

The original screws are just long enough to securely hold the horn itself.
Maybe you could update the assembly instructions with an updated screw length (and required screw type)

nikolaif399, 2019-01-07:
We've had the same issue. We ended up using a different screw than the 10mm m3 button head, we'll update the instructions when we have a better solution. Thank you for bringing this to our attention.

jjoepayne, 2019-01-07:
Thanks for pointing out the issue, I'd recommend these bolts for the middle leg shafts:

https://www.mcmaster.com/92005a078

I will update the instructions and purchasing list to match this, thanks again!

Closed 2019-01-07.

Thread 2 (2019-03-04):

Two different screws, nuts, and spacers

fdavulcu, 2019-03-04:
In [HardwareList](https://github.com/robomechanics/MiniRHex/tree/master/HardwareList), there are two files: MiniRhexHardware.xlsx and readme.md. In these files, the screws, nuts, and spacers are different:

| Part    | readme.md                               | MiniRhexHardware.xlsx                      |
|---------|-----------------------------------------|--------------------------------------------|
| Screws  | M3 x 0.5mm Thread, 10mm Long            | M2.5 x 0.45 mm Thread, 16 mm Long          |
| Nuts    | M3 x 0.5 mm Thread                      | M2.5 x 0.45 mm Thread                      |
| Spacers | 4.5 mm OD, 3 mm Long, for M3 Screw Size | 4.5 mm OD, 10 mm Long, for M2.5 Screw Size |

Which file is the correct one?

nikolaif399, 2019-03-04:
Hey Furkan,
The readme.md file is correct, we're using m3 hardware. I removed the old file, thanks for bringing this to our attention!

Closed 2019-03-04.

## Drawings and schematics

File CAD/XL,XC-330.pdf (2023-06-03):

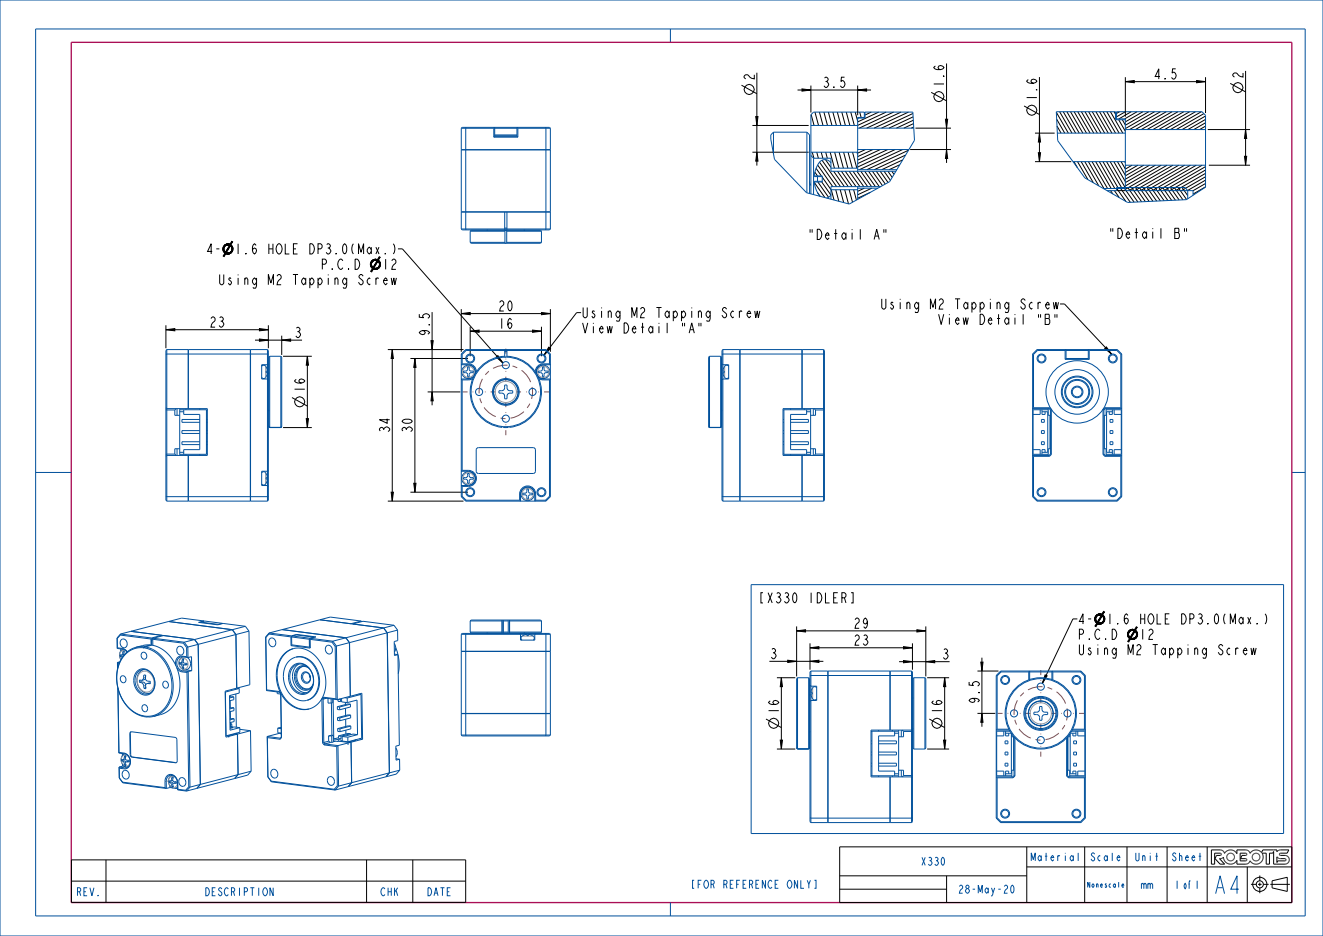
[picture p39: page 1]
28-May-20; Nonescale; Material; Scale; Unit; Sheet; REV.; DESCRIPTION; CHK; DATE; "Detail; [X330 IDLER]; 4- 1.6 HOLE DP3.0(Max.); View Detail

Using M2 Tapping Screw

4- 1.6 HOLE DP3.0(Max.)

[FOR REFERENCE ONLY]

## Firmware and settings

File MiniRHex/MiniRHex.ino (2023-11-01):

#include "leg_info.h"
#include "control_parameters.h"
#include "desired_values.h"
#include "pd_control.h"
#include "gait_parameters.h"

#include <DynamixelShield.h>
#include <WiFiNINA.h>

DynamixelShield dxl;
using namespace ControlTableItem;

// Sync read/write structs
ParamForSyncWriteInst_t sync_write_param;
ParamForSyncReadInst_t sync_read_param;
RecvInfoFromStatusInst_t read_result;

// Rewritable globals
float desired_vel;
float desired_theta;
float actual_vel;
float actual_theta;
float control_signal;
float actual_p;

// Legs setup
const int legs_active = 6;

// Motor values
float present_velocity[legs_active+1];
float present_position[legs_active+1];
float goal_velocity[legs_active+1];

// Battery status
bool flash;         // LED on or off
bool shutdown;      // Disable motor movement
int voltage;        // Current battery voltage
int voltage_check;  // Current motor voltage

bool wifi;          // WiFi connection active

void setup() {
  Serial.begin(57600);                             // set the Serial Monitor to match this baud rate
  dxl.begin(57600);                                // 57600 is the default baud rate for XL330 motors
  dxl.setPortProtocolVersion(2.0);                 // XL330 motors use protocol 2
  
  pinMode(LED_BUILTIN, OUTPUT);                    // setup LED
  int t_start = millis();
  for (int i = 1; i <= legs_active; i++) {         // legs stored at their index
    dxl.torqueOff(legs[i].id);
    dxl.setOperatingMode(legs[i].id, OP_VELOCITY); // change servo to wheel mode
    dxl.writeControlTableItem(RETURN_DELAY_TIME, legs[i].id, 0);
    dxl.torqueOn(legs[i].id);
    update_gait(i, initial_gait, t_start);         // set initial parameters, initial_gait in gait_parameters
  }

  sync_write_param.id_count = legs_active;         // set sync read/write motor IDs
  sync_read_param.id_count = legs_active;
  for (int i=1; i<=legs_active; i++) {
    sync_write_param.xel[i-1].id = legs[i].id;
    sync_read_param.xel[i-1].id = legs[i].id;
  }

  begin_wifi();
}

void jump_ready() {
  int t_start = millis();
  for (int i = 1; i <= legs_active; i++) {
    legs[i].desired_theta = 90;
    update_gait(i, STAND, t_start);
  }
  Serial.println("JUMP READY");
}

void jump() {

  int t_start = millis();
  while (millis() - t_start < 900) {
    Serial.println(t_start - millis());
    if (millis() - t_start > 0) {
      dxl.setGoalVelocity(legs[1].id, 100, UNIT_PERCENT);
      dxl.setGoalVelocity(legs[4].id, -100, UNIT_PERCENT);
    }
    if (millis() - t_start > 100) {
      dxl.setGoalVelocity(legs[2].id, 100, UNIT_PERCENT);
      dxl.setGoalVelocity(legs[5].id, -100, UNIT_PERCENT);
    }
    if (millis() - t_start > 190) {
      dxl.setGoalVelocity(legs[3].id, 100, UNIT_PERCENT);
      dxl.setGoalVelocity(legs[6].id, -100, UNIT_PERCENT);
    }
  }
  for (int i = 1; i <= legs_active; i++) {
    legs[i].desired_theta = 0;
    update_gait(i, STAND, t_start);
  }
}

int count = 0;
int t = 0;
void loop() {
  // loop counter
  count++;

  // Every 10 loop iterations, find max voltage supplied to each leg and compare with nominal
  if (count % 10 == 0) {
    voltage = 0;
    for (int i = 1; i <= legs_active; i++) {
      voltage_check = dxl.readControlTableItem(PRESENT_INPUT_VOLTAGE, legs[i].id);
      if (voltage_check > voltage) voltage = voltage_check;
    }
    Serial.print("Voltage: ");
    Serial.print(voltage/10.0);
    Serial.print(", Frequency: ");
    Serial.print(10000/(millis()-t));
    Serial.println("Hz");
    t = millis();

    bool update = false;
    if (voltage > 45) {
      if (flash) update = true;
      flash = false;            // off (safe voltage)
      shutdown = false;
    }
    else if (voltage > 40) {
      if (!flash) update = true;
      flash = true;             // on (low voltage)
      shutdown = false;
    }
    else {
      if (!flash) update = true;
      flash = true;             // shutdown motors (very low voltage)
      shutdown = true;
    }

    if (update) {
      for (int i = 1; i <= legs_active; i++) {
        if (flash) {
          dxl.ledOn(legs[i].id);
        } else {
          dxl.ledOff(legs[i].id);
        }
      }
    }
  }

  // teleop control
  if (Serial.available() || wifi) {
    char a;
    if (Serial.available()) {
      a = (char)(Serial.read());
    } else {
      a = update_wifi();
    }
    int gait = -1;
    switch (a) {
      case 'q': // stand
        gait = STAND;
        break;
      case 'w': // forwards
        gait = WALK;
        break;
      case 'a': // left
        gait = LEFT;
        break;
      case 's': // reverse
        gait = REVERSE;
        break;
      case 'd': // right
        gait = RIGHT;
        break;
      case 'e': // pronk
        gait = PRONK;
        break;
      case 'r': // run
        gait = RUN;
        break;
      case 'x': // prepare jump
        jump_ready();
        break;
      case 'j': // jump
        jump();
        break;
    }

    if (gait != -1) {
      int t_start = millis();
      for (int i = 1; i <= legs_active; i++) {
        update_gait(i, gait, t_start);
      }
    }
  }

  // primary for-loop
  sync_read_position();
  sync_read_velocity();
  for (int i = 1; i <= legs_active; i++) {
    actual_theta = present_position[i]; // degrees
    actual_vel = present_velocity[i];   // degrees/millisecond
    if (!legs[i].deadzone) {
      if (legs[i].gait == STAND) { // standing or sitting
        if (legs[i].right_side) {
          desired_theta = -legs[i].desired_theta;
        }
        else {
          desired_theta = legs[i].desired_theta;
        }
        actual_theta = actual_theta - legs[i].zero; // zero out leg thetas, accounts for small servo irregularities
        control_signal = pd_controller(actual_theta, desired_theta, actual_vel, 0, kp_hold, kd_hold);
      } else if (legs[i].gait == RUN){
        float v = 20;
        control_signal = v*(-legs[i].right_side*2+1) - actual_vel;
      }
      else { // walking, turning
        // compute absolute desired values (theta and velocity) from clock time
        vals v = get_desired_vals(millis(), legs[i]);
        // translate theta and v to relative (left and right)
        if (legs[i].right_side) {
          desired_vel = -v.global_velocity; // relative
          desired_theta = -v.global_theta; // relative
        }
        else { // left side, relative is same as global
          desired_vel = v.global_velocity;
          desired_theta = v.global_theta;
        }
        actual_theta = actual_theta - legs[i].zero;

        control_signal = pd_controller(actual_theta, desired_theta, actual_vel, desired_vel, legs[i].kp, legs[i].kd);
      }
      float new_vel = actual_vel + control_signal;
      if (shutdown) {
        goal_velocity[i] = 0;
      } else {
        goal_velocity[i] = new_vel;
      }
    }
  }
  sync_write_velocity();
}

void sync_read_velocity() {
  sync_read_param.addr = 128; // Present Velocity of DYNAMIXEL-X series
  sync_read_param.length = 4;
  dxl.syncRead(sync_read_param, read_result);
  int raw;
  for (int i=1; i<=legs_active; i++) {
    memcpy(&raw, read_result.xel[i-1].data, read_result.xel[i-1].length);
    present_velocity[i] = raw * .06 * 0.229;
  }
}

void sync_read_position() {
  sync_read_param.addr = 132; // Present Position of DYNAMIXEL-X series
  sync_read_param.length = 4;
  dxl.syncRead(sync_read_param, read_result);
  int raw;
  for (int i=1; i<=legs_active; i++) {
    memcpy(&raw, read_result.xel[i-1].data, read_result.xel[i-1].length);
    present_position[i] = raw * 0.088;
  }
}

void sync_write_velocity() {
  sync_write_param.addr = 104; // Goal Velocity of DYNAMIXEL-X series
  sync_write_param.length = 4;
  for (int i=1; i<=legs_active; i++) {
    int raw = goal_velocity[i] / .06 / 0.229;
    memcpy(sync_write_param.xel[i-1].data, &raw, 4);
  }
  dxl.syncWrite(sync_write_param);
}

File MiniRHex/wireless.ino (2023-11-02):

/*
  Based on the "Web Server Access Point (AP) Mode with MKR WiFi 1010" tutorial
  https://docs.arduino.cc/tutorials/mkr-wifi-1010/web-server-ap-mode
*/

#include <WiFiNINA.h>
#include <utility/wifi_drv.h>

char ssid[] = "minirhex";
WiFiServer server(80);
const int RED = 25;
const int GREEN = 26;
const int BLUE = 27;

void begin_wifi() {
  WiFiDrv::pinMode(GREEN, OUTPUT);
  WiFiDrv::pinMode(RED, OUTPUT);
  WiFiDrv::pinMode(BLUE, OUTPUT);
  WiFiDrv::analogWrite(GREEN, 0);
  WiFiDrv::analogWrite(RED, 0);
  WiFiDrv::analogWrite(BLUE, 0);

  if (WiFi.status() == WL_NO_MODULE) {
    Serial.println("No WiFi module present");
    return;
  }
  if (WiFi.firmwareVersion() < WIFI_FIRMWARE_LATEST_VERSION) {
    Serial.println("Please upgrade the WiFi firmware");
  }
  WiFi.config(IPAddress(10, 0, 0, 1));
  if (WiFi.beginAP(ssid) != WL_AP_LISTENING) {
    Serial.println("Creating WiFi network failed");
    return;
  }
  server.begin();
  wifi = true;

  Serial.print("SSID: ");
  Serial.println(WiFi.SSID());
  Serial.print("Website: http://");
  Serial.println(WiFi.localIP());
}

char update_wifi() {
  if (WiFi.status() == WL_AP_LISTENING) {
    WiFiDrv::analogWrite(RED, 0);
    WiFiDrv::analogWrite(GREEN, 20);
    WiFiDrv::analogWrite(BLUE, 0);
  } else if (WiFi.status() == WL_AP_CONNECTED) {
    WiFiDrv::analogWrite(RED, 0);
    WiFiDrv::analogWrite(GREEN, 0);
    if (millis() % 250 > 125) {
      WiFiDrv::analogWrite(BLUE, 20);
    } else {
      WiFiDrv::analogWrite(BLUE, 0);
    }
  } else {
    WiFiDrv::analogWrite(RED, 20);
    WiFiDrv::analogWrite(GREEN, 0);
    WiFiDrv::analogWrite(BLUE, 0);
  }
  WiFiClient client = server.available();   // listen for incoming clients
  char output = 0;
  if (client) {                             // if you get a client,
    String currentLine = "";                // make a String to hold incoming data from the client
    while (client.connected()) {            // loop while the client's connected
      if (client.available()) {             // if there's bytes to read from the client,
        char c = client.read();             // read a byte, then
        if (c == '\n') {                    // if the byte is a newline character
          if (currentLine.length() == 0) {  // empty line is end of http request
            display_website(client);        // display the webpage
            break;
          } else {
            currentLine = "";    // clear currentLine
          }
        }
        else if (c != '\r') {    // if you got anything else but a carriage return character,
          currentLine += c;      // add it to the end of the currentLine
          if (currentLine.substring(currentLine.length() - 6, currentLine.length() - 1) == "GET /") {
            output = currentLine[currentLine.length() - 1]; // return the command
          }
        }
      }
    }
    client.stop();                                   // close the connection
  }
  if (output == ' ') output = 'q';                   // space is also e-stop
  return (output);
}

void display_website(WiFiClient client) {
  // HTTP headers
  client.println("HTTP/1.1 200 OK");
  client.println("Content-type:text/html");
  client.println();

  // Controls
  client.print("<div style=\"display:inline-grid; grid-template-columns: 70px 70px 70px; grid-template-rows: 70px 70px 70px 70px;\">");
  client.print("<b></b><button onclick=\"window.location.href='/r';\">Run<br>(r)</button><b></b>");
  client.print("<b></b><button onclick=\"window.location.href='/w';\">Forward<br>(w)</button><b></b>");
  client.print("<button onclick=\"window.location.href='/a';\">Left<br>(a)</button>");
  client.print("<button onclick=\"window.location.href='/q';\">Stop<br>(space/q)</button>");
  client.print("<button onclick=\"window.location.href='/d';\">Right<br>(d)</button>");
  client.print("<b></b><button onclick=\"window.location.href='/s';\">Reverse<br>(s)</button>");
  client.print("</div><br><br>");

  // Key listener
  client.print("<script>");
  client.print("document.onkeydown = function(evt) {");
  client.print("evt = evt || window.event;");
  client.print("window.location.href = \"/\"+evt.key;");
  client.print("};");
  client.print("</script>");

  // Terminate http response
  client.println();
}

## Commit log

2018-05-18 Added CAD Files and Images
    [Battery and case.SLDASM, Battery case.SLDPRT, Battery.SLDPRT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]
2018-05-19 Assembly Instructions Update
2018-05-23 Updated Assembly Instructions
    Changed link to assembly instructions
    More verbose description of configuration process
2018-05-23 Updated link for assembly instructions
2018-06-28 Updated for M3 hardware and better fits
    [Battery case.SLDPRT, base.SLDPRT, leg.SLDPRT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]
2018-06-28 updated to M3 hardware
    [MiniRhexHardware.xlsx]
2018-06-28 updated with new components
    [fullMiniRhex.SLDASM]
2018-09-09 updated setting servo id instructions
2018-09-25 updated appearance and added quantity needed per robot
    [MiniRhexHardware.xlsx]
2018-10-09 Added STL folder for printing
    [servo sleeve.stl]
2018-10-09 Added stls for printing
    [Battery case.STL, leg.STL, servo sleeve.STL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]
2018-10-09 made slightly taller for better fit
    [servo sleeve.SLDPRT]
2018-10-09 Added 3d printing tips
2018-11-13 m3 clearance holes
    [base.DXF]
2018-11-27 gcode to print full robot
2018-11-27 changed location of assembly instructions
2018-11-27 Update and rename assembly_instructions to assembly_instructions.md
2018-11-27 added servo id and zero headers
2018-11-29 updated servo ids and zeros instructions
2018-11-30 added printing cost estimate
2018-11-30 moved printing description to link column
2018-11-30 re upload excel sheet
    [MiniRhexHardware.xlsx]
2018-11-30 Transfer origin/release into origin/master
    [MiniRhexHardware.xlsx]
2019-01-07 Adding Screws for Servo Horns
    Resolution to https://github.com/robomechanics/MiniRHex/issues/1
2019-01-07 Adding Screws for Servos
    resolution to https://github.com/robomechanics/MiniRHex/issues/1
    [MiniRhexHardware.xlsx]
2019-01-07 Editing instructions to include new bolts
    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
2019-03-04 Removed old MiniRHex hardware file
    [MiniRhexHardware.xlsx]
2019-03-23 Update readme.md
    Updated the 3-D printing section to be more explicit and specific.
2019-03-23 Update readme.md
    Updated a clearer image of the main board power pin placement
2019-03-23 uploaded a clearer picture of the power pins on the main board
2019-03-23 added new power pin image to assembly file
2019-03-23 Update readme.md
    Updated picture and added expected PLA amount used for printing.
2019-03-23 Update README.md
    Updated configuring servo IDs.
2019-03-23 Update readme.md
    Need to be more specific on what supports inside the 3D printed part.
2019-03-25 added new pictures for readme assembly
2019-07-09 uploading image to clarify slot placement
2019-07-09 added clarification for slot placement
2019-07-09 added better clarification for slot placement
2020-01-17 Updated screws, added battery strap in BOM
2020-01-17 Updated number of screws
2020-01-17 Updated screws
2020-01-17 Updated directions with new screw lengths, additional detail
2020-01-17 Updated CAD with small tweaks to make assembly easier
    Widened base plate to better accommodate battery wires, fixed size of nut capture hex holes, added strap to battery holder, raised base of battery holder so screws don't run into battery.
    [Battery case.SLDPRT, Dynamixel XL-320.SLDPRT, base.SLDPRT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]
2020-01-17 Added battery strap
2020-01-17 Updated STLs with minor tweaks to make assembly easier
    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
    [Battery case.STL, base.DXF, servo sleeve.STL]
2022-07-14 Update Arduino price and link
2022-07-29 Added code for running minirhex with new motors on arduino
    all six motors run in alternating tripod gait, but three are at different speeds than other three
2022-09-09 Fixed voltage reading
2022-10-14 Added servo ID setting instructions
2023-02-17 Simple velocity-controlled running gait
2023-02-24 Fixed Arduino Shield link
2023-09-25 One screw files for outreach
    [hub_one_screw.SLDPRT, leg_one_screw.SLDPRT]
2023-10-27 Updating assembly instructions
2023-10-28 Add voltage monitor to hardware list
2023-10-28 Added LiPo safe bag
2023-10-28 Finished updating assembly instructions
2023-10-28 Moved servo ID setting to assembly instructions
2023-10-28 Updating motor ID image
2023-10-29 Updated leg CAD
    [leg_full.SLDPRT, long_hub.SLDPRT, minirhex_assembly.SLDASM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]
2023-10-29 Updated STL links
2023-10-30 Added voltage monitor image
2023-10-31 Updated leg geometry
    [minirhex_assembly.SLDASM, quick_connect_leg.SLDPRT, quick_connect_leg_left.STL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]
2023-10-31 Revert "One screw files for outreach"
    This reverts commit 2e8af682ab93c8c9e30c1696e022bf98d52f2f73.
    [hub_one_screw.SLDPRT, leg_one_screw.SLDPRT]
2023-10-31 Revert "Add files via upload"
    This reverts commit f923d8a8641890806b6456ed2107a162077c41cb.
    [cmu-wordmark-horizontal-k.dxf, dxl_XL-330.SLDPRT, leg_full.SLDPRT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]
2023-11-01 Switching to relative links
2023-11-02 Added LED indicator for WiFi and updated instructions
